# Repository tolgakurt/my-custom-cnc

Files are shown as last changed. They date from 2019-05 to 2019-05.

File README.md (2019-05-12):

# Yet Another CNC Milling Machine

Some time ago I decided that I need a CNC milling machine that would mainly be able to etch and drill PCBs, so that I can prototype faster when building circuits. There were already available, cheap, and similar CNC machines for this purpose, however, most of them had weak spindles and slender frame members which are suitable only to machine PCB materials or acrylic, but I also wanted to machine some other materials as well. There were also some professional grade machines for this purpose, but they were either expensive and overqualified, or didn't meet the specs I required. And most importantly, as a machinery enthusiast I wanted to build one from scratch for fun. Here, I'll try to present my not-so-original design for such a machine.  

## Overall Design

The frame design is very much like those cheap Chinese routers such as [this one](https://www.banggood.com/CNC2418-3-Axis-Mini-DIY-CNC-Router-USB-Wood-Carving-Engraving-Machine-p-1239336.html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). Most of the machines offered by Chinese vendors come with 775 or 755 model spindles which are rated in between 60W and 150W. I wanted the machine to be able to mill other materials like MDF, hard plastics (like PA, PE, POM, etc.), and low grade aluminum. Thus my first modification was to use a [stronger spindle of 400W](https://www.banggood.com/12-48V-400W-ER11-Air-Cooled-Engraver-Spindle-Motor-for-CNC-Carving-p-1269291.html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). Additionally, these routers are mostly built with 20mm by 20mm aluminum Sigma profiles. Since I'll be using a stronger spindle and machining more rigid materials, I went with 30mm by 60mm and 30mm by 30mm sections mostly. Here is the overall view of the machine:  

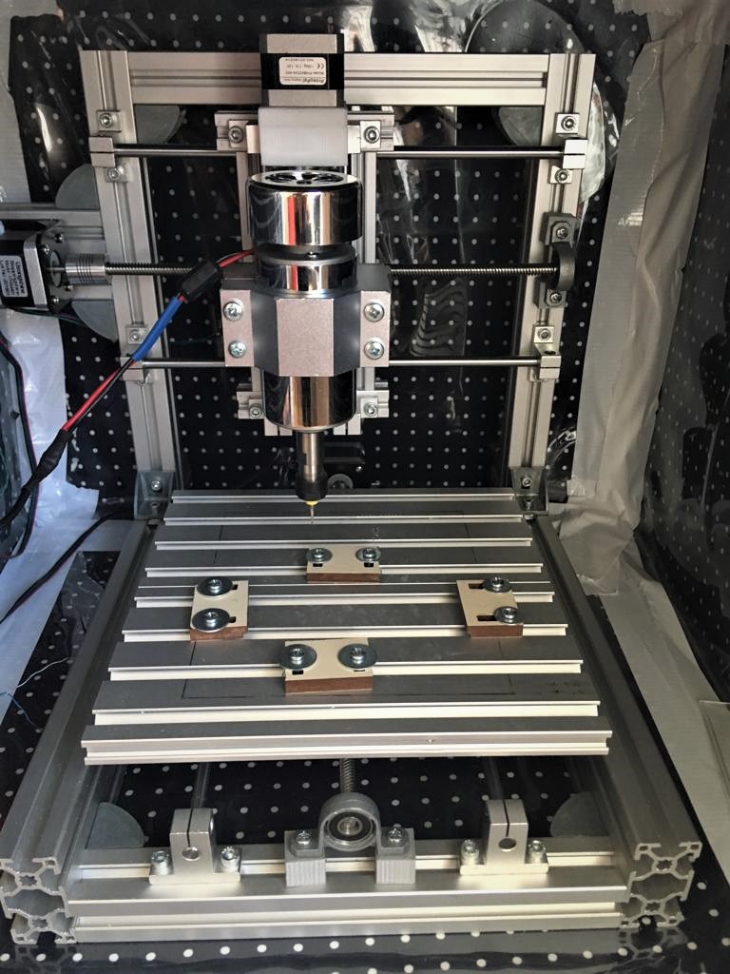
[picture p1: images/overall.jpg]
Overall View


This design offers 20cm by 20cm working area and 10cm of working depth.  

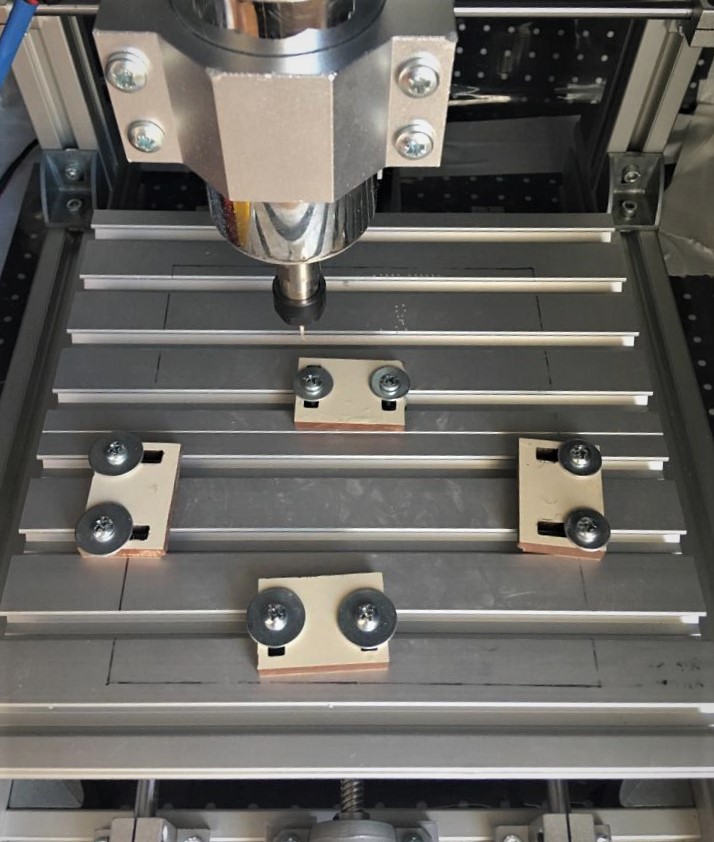
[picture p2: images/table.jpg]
Working Area


The system is mobilized by NEMA17 (specifically 42HS4401) stepper motors, which are driven by A4988 modules embedded into the combination of [an Arduino Uno and a CNC shield](http://osoyoo.com/2017/04/arduino-uno-cnc-shield-v3-0-a4988/). However, I didn't connect the spindle control to the Uno yet, but simply built a box that contains a switch to power it on/off (other switch is for the 3D printer) and adjust the speed manually. One important thing here is that I modified all axes for half steps. This is achieved by connecting some jumpers onto the CNC shield. The details are explained in the link above. The reason of half stepping is to get a better resolution as well as silencing the stepper motors. Half stepping torque of stepper motors is given as 75% of full stepping, so not much loss there. Quarter stepping will make it more silent and accurate, however the torque will decrease around 35% which is too much.  

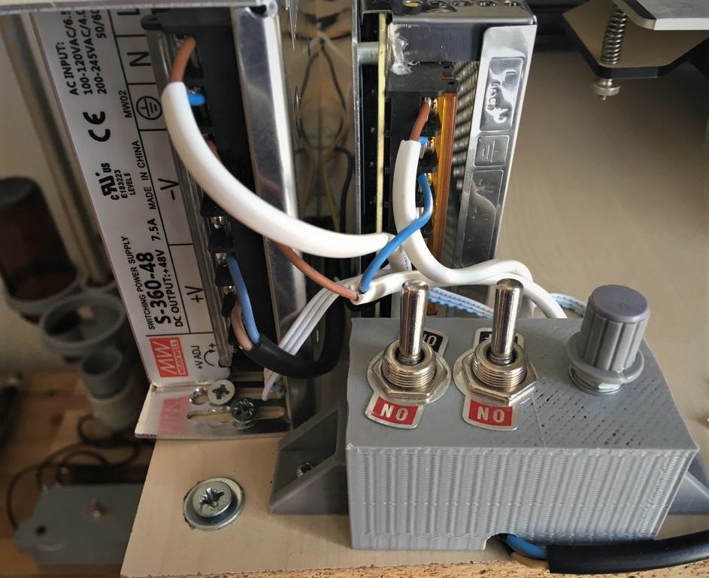
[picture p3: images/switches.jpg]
Switch Box


There are already available 3D printed cases to hold both the Arduino Uno and mentioned shield, and I used [this one](https://www.thingiverse.com/thing:2808019). The case is put outside the enclosed box, since A4988 modules can get dangerously hot inside. I mounted an 8cm fan on top of this case for the same reason. And don't forget to attach tiny heat sinks on top of A4988 modules.  

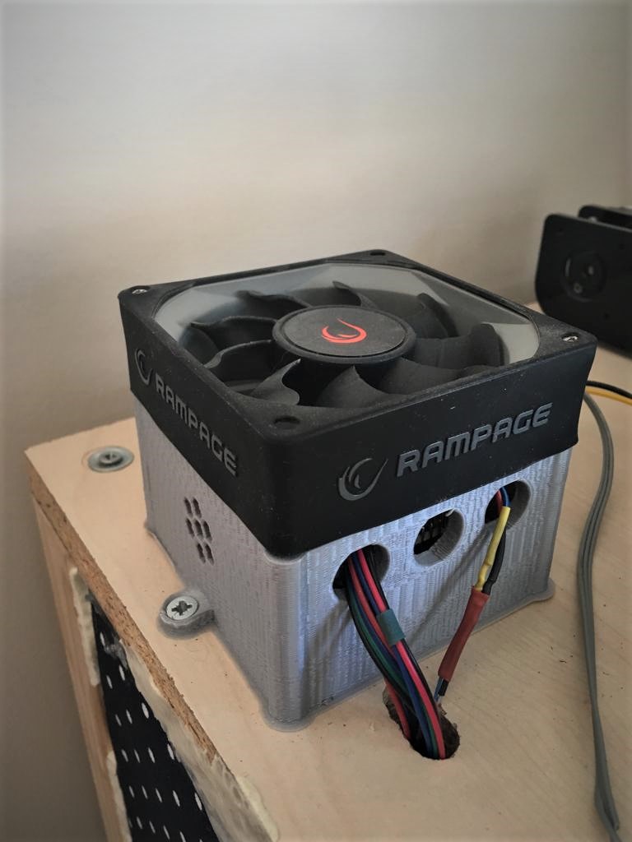
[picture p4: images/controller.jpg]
Case of the Arduino Uno and the CNC Shield


And when all was finished, I realized that the machine makes too much noise to work at night in an apartment. So, I built an ugly-looking, but well-functioning box for sound isolation. It is simply a box with 60cm by 60cm OSB plates, connected with 60cm square wooden legs. Then 6 sides are enclosed by 6 Bondex plates (which is a laminated material with layers foam + rubber + foam as can be seen [here](https://www.adanasesizolasyonu.com/wp-content/uploads/2018/03/Bondex-S%C3%BCnger222.jpg)). I also coated Bondex plates with fabric (as if it's gonna look better) and flexible plastic sheets (so that I can collect the dirt after a milling operation easily). This worked well, except that the machine vibrates the surroundings, so that some noise is regenerated outside the box. What I did was to use some stiff foam as an isolator beneath the box which damped the vibration considerably. According to my phone measurements, the booth drops the noise by 30db, which is enough to keep my neighbors happy.  

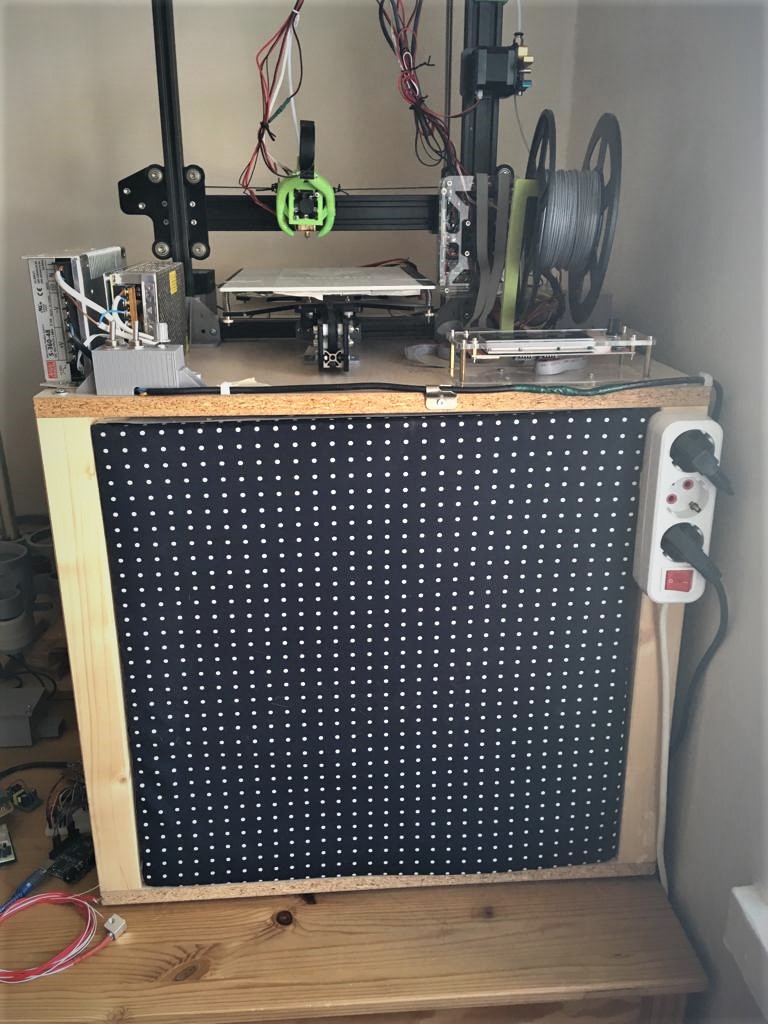
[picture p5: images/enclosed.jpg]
Isolation Booth


And it looks like this in my workshop:  

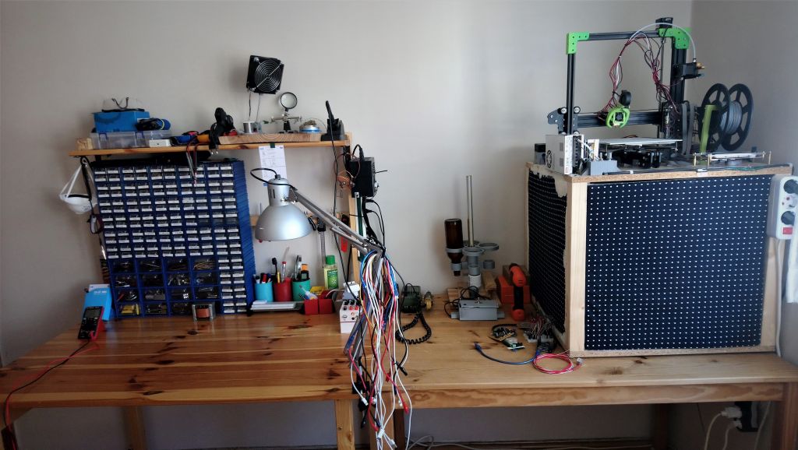
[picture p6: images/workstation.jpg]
My Workshop


## Bill of Materials

### Frame

2x 38cm long [sigma profiles with 30mm by 60mm sections](https://tr.aliexpress.com/item/3D-End-striyel-al-minyum-ala-m-Profil-3060-W-A-r-Al-minyum-3060-W/32987773308.html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)  
3x 25.5cm long [sigma profiles with 30mm by 30mm sections](https://tr.aliexpress.com/item/3D-Yaz-c-Par-alar-3030-Al-minyum-Profil-Avrupa-Standart-Eloksal-Lineer-Ray-Al-minyum/32968908166.html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)  
4x 8.5cm long sigma profiles with 30mm by 30mm sections  
2x 10cm long [sigma profiles with 20mm by 20mm sections](https://tr.aliexpress.com/item/CNC-3D-Printer-Parts-4pcs-lot-European-Standard-Anodized-V-Slot-Linear-Rail-Aluminum-Profile-Extrusion/32813616949.html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,searchweb201602_8_10065_10068_319_10059_10884_317_10887_10696_321_322_10084_453_10083_454_10103_10618_10307_537_536,searchweb201603_52,ppcSwitch_0&algo_expid=79a273b7-c577-4c55-8660-7f41bd6c1b0e-2&algo_pvid=79a273b7-c577-4c55-8660-7f41bd6c1b0e&transAbTest=ae803_4)  
4x 14cm long sigma profiles with 20mm by 20mm sections  
2x 24cm long [sigma profiles with 15mm by 120mm sections](http://www.sigmaprofil.net/15x120-sigma-profile)  
14x [corner connectors for 30mm sigmas](https://tr.aliexpress.com/item/10pcs-of-3030-Corner-Fitting-Angle-30x30-Decorative-Brackets-Aluminum-Profile-Accessories-L-Connector-Fasten-connector/32669590916.htm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,searchweb201602_8_10065_10068_319_10059_10884_317_10887_10696_321_322_10084_453_10083_454_10103_10618_10307_537_536,searchweb201603_52,ppcSwitch_0&algo_expid=9d5dbc37-118d-4f2e-b263-79113ac94142-9&algo_pvid=9d5dbc37-118d-4f2e-b263-79113ac94142&transAbTest=ae803_4)  
4x [corner connectors for 20mm sigmas](https://tr.aliexpress.com/item/10-pcs-25-pcs-al-minyum-2020-k-e-parantez-tertibatlar-20x20x17mm-k-e-a-braketi/32922071230.html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)  

### Rails

2x 18cm long [M8 linear shafts for Z axis](https://www.banggood.com/Outer-Diameter-8mm-x-300380400500mm-Cylinder-Liner-Rail-Linear-Shaft-Optical-Axis-p-993100.html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)  
4x 30cm long M8 linear shafts for XY axes  
1x 18cm long 1.25mm step M8 lead screw for Z axis  
2x 30cm long [8mm step M8 lead screw for XY axes](https://www.banggood.com/T8-8mm-1000mm-Stainless-Steel-Trapezoidal-Lead-Screw-For-3D-Printer-p-1146127.html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)  
12x [SK08 shaft supports](https://aliexpress.com/item/SK08-SK-STAND-UP-Shaft-Support/582520990.html)  
3x [KP08 bearing for lead screw ends](https://tr.banggood.com/8mm-Bore-Diameter-Pillow-Block-Mounted-Ball-Bearing-KP004-Zinc-Alloy-p-976258.html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)  
3x [5mm to 8mm flexible couplings for NEMA17](https://tr.aliexpress.com/item/5-adet-grup-3d-yaz-c-aksesuarlar-5x8mm-veya-5x5mm-z-eksen-Nema-17-23-Step/32840459829.html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)  
3x [M8 anti-backlash nuts for lead screws](https://tr.aliexpress.com/item/T8-Anti-Backlash-Spring-Loaded-Nut-Elimination-Gap-Nut-for-8mm-Acme-Threaded-Rod-Lead-Screws/32808521751.html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,searchweb201602_8_10065_10068_319_10059_10884_317_10887_10696_321_322_10084_453_10083_454_10103_10618_10307_537_536,searchweb201603_52,ppcSwitch_0&algo_expid=3690f36e-8d57-4c15-9ed8-b457cb2fba50-0&algo_pvid=3690f36e-8d57-4c15-9ed8-b457cb2fba50&transAbTest=ae803_4)
8x [LM8UU linear bearings](https://www.banggood.com/LM8UU-8mm-Linear-Ball-Bearing-Bush-Steel-for-CNC-Router-Mill-Machine-p-906777.html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)  
4x [PTFE coated 8mm diameter, 15 mm long linear bearings](https://www.rulmanmarketi.com/urun/pap-0815-p10-teflon-burc-8x10x15-permaglide-burc-3459)  

### Nuts and Bolts

Lots of 10mm long M5 bolts  
Lots of M5 T-nuts for 3030 profile  
Lots of 8mm long M4 bolts  
Lots of M4 T-nuts for 2020 profile  

### Motors
3x NEMA17 stepper similar to [that](https://tr.banggood.com/JKM-42-Hybrid-Stepper-Motor-2-Phase-1_840MM-For-CNC-Router-p-933548.html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)  
2x [NEMA17 motor mounts](https://tr.aliexpress.com/item/NEMA-17-Steppr-Motor-Aksesuarlar-Braketi-Destek-Montaj-L-Tipi-Braketi-Da-42-Step-Motor-Stepping/32919542128.html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)  
1x [400W air cooled spindle motor, clamp, and PS](https://www.banggood.com/400W-12000rpm-ER11-Chuck-CNC-Brushless-Spindle-Motor-with-Driver-Speed-Controller-and-Clamp-p-1149321.html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)  

### Controller
1x [Arduino Uno](https://store.arduino.cc/usa/arduino-uno-rev3)  
1x [Arduino CNC Shield](https://tr.aliexpress.com/item/CNC-kit-for-arduino-CNC-Shield-V3/32829060574.html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,searchweb201602_0_10084_10083_10887_10307_321_453_322_454_10618_536_10065_317_537_10068_319_10059_10103_10884_10696,searchweb201603_0,ppcSwitch_0&algo_pvid=94aba3e1-d1bb-4407-9ae0-063b6d83051e&algo_expid=94aba3e1-d1bb-4407-9ae0-063b6d83051e-0)  
3x [A4988 driver modules](https://tr.aliexpress.com/item/Aokin-A4988-S-r-c-Mod-l-i-in-So-utucu-ile-Step-Motor-S-r/32951539408.html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)  
1x [12V 100W PS for controller and the stepper motors](https://www.banggood.com/AC-220V-To-DC-12V-10A-120W-Power-Supply-Lighting-Transformer-Adapter-Driver-For-Strip-Light-Lamp-p-1145387.html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)  

## Custom Parts

You need to 3D print the parts in the `printedParts` directory. These parts are dimensioned to fit the other parts like SK08, KP08, L8UU, etc.  

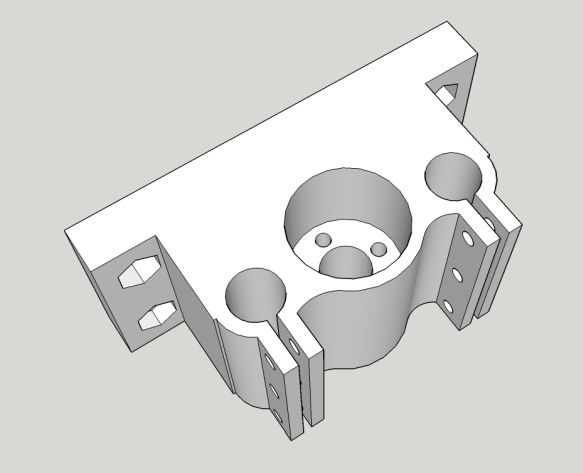
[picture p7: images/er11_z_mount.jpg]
Spindle Clamp Mount


Moving part in Z axis: This part connects the lead screw nut and PTFE coated bearings to the spindle clamp.  

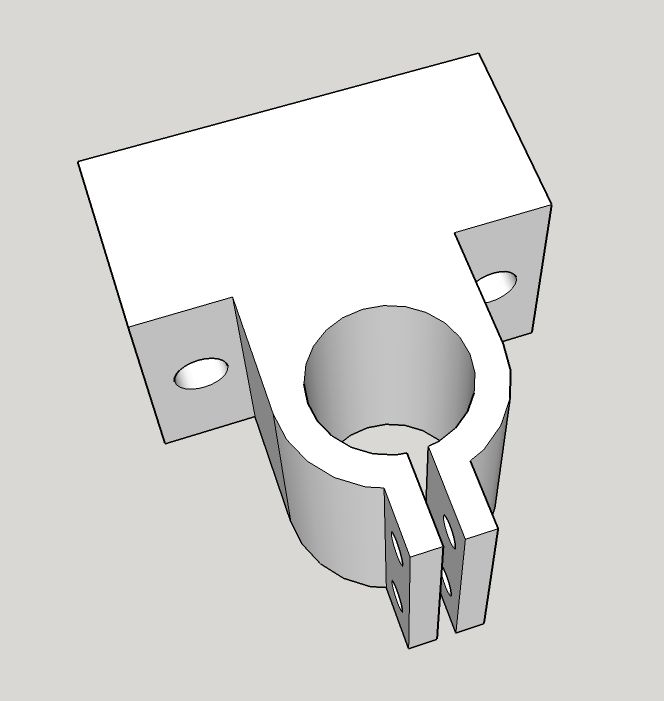
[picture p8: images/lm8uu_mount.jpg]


This part connects LM8UU bearings to the sigma profiles they need to connect to. You should print 8 of these.  

## Assembly

I wish that I can shoot a video that shows the assembly. But it'll be very similar to [this](https://www.youtube.com/watch?v=hB4Cvbtu-lA) or [that](https://www.youtube.com/watch?v=P-zZxicjNww). I'm not sure, maybe some day.  

## Installing Software and Suggested Settings to Operate the Machine

Arduino Uno hosts [GRBL software](https://github.com/grbl/grbl) which routes the machine. To operate the machine from my computer, I use [bCNC](https://github.com/vlachoudis/bCNC), since it's not a gcode sender only, but does offer nice features like probing, autoleveling, gcode editing within a functional user interface.  

The settings I use when I am machining PCB materials is as such:  

Etching feed rates: XY = 250mm/min, Z = 100mm/min  
Z-down when etching: -0.15mm for 30 degree V-bit  

Drill feed rates: Z = 100mm/min  
Drill depth: -1.8mm (or PCB thickness - 0.3mm)

Milling feed rates: XY = 150mm/min, Z = 100mm/min  
Milling depth: -1.5mm (if only perimeter will be milled)  
Milling depth: -0.5mm (if an inner path will be milled)  

## Pictures

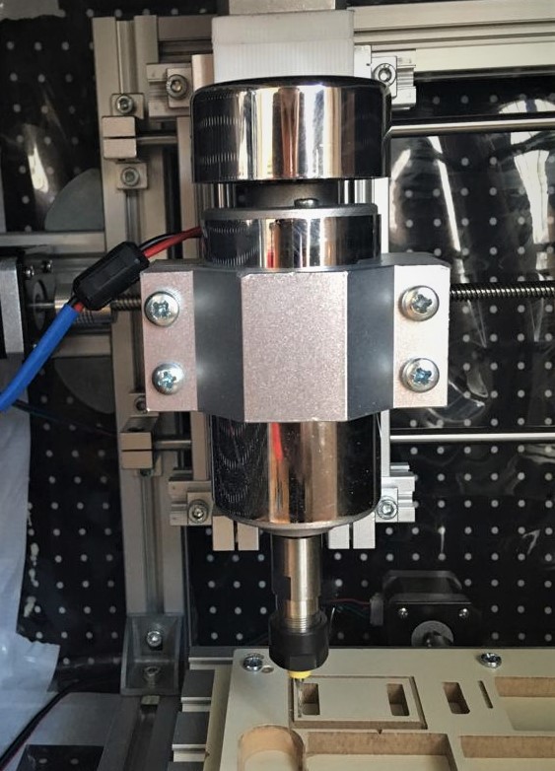
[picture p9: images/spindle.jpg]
Spindle Close-up


Close-up to the spindle.  

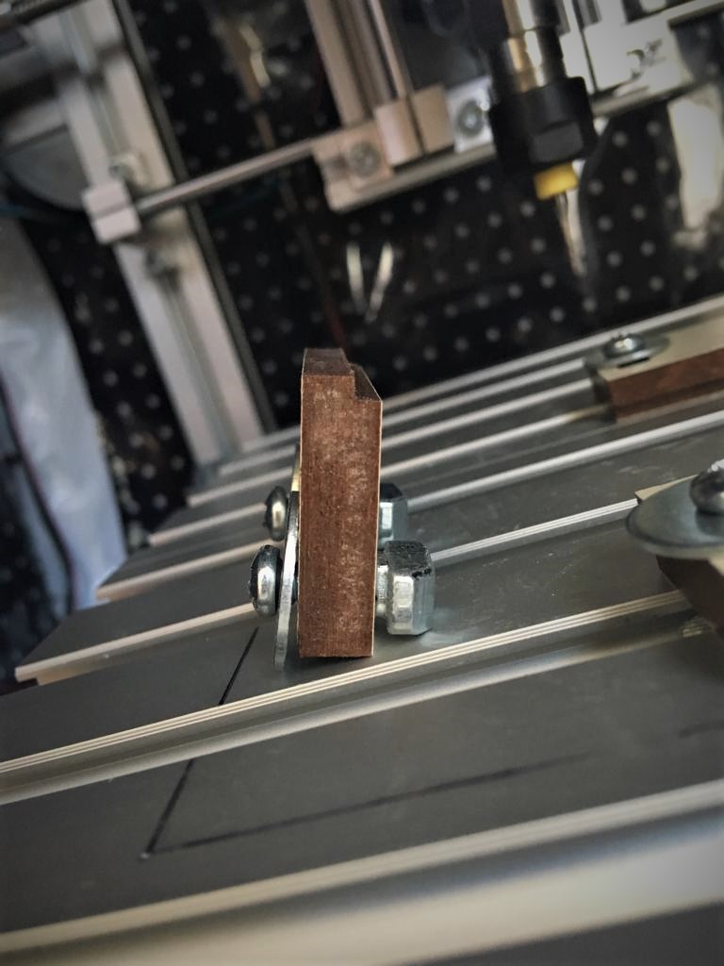
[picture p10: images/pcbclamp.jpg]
PCB Clamps


The clamps I machined out of MDF for PCBs. These clamps have a 3mm cavity to press two PCBs. Why two PCBs? Well, if we use a single PCB put directly above the table and we set the drill depth to 1.5mm, the holes will barely be complete. It's a good practice to drill a bit more than needed to get clean holes. However, if we drill more, the aluminum table will be full of holes soon; and the drill bits may get damages since they are delicate. So, I put a PCB onto another PCB with the same size (the thickness becomes 3mm, thus the cavity in the clamp), and drill down to 1.8mm. So I have collection of dummy PCBs for some common sizes (like 5cm by 10cm, 10cm by 10cm, etc.).  

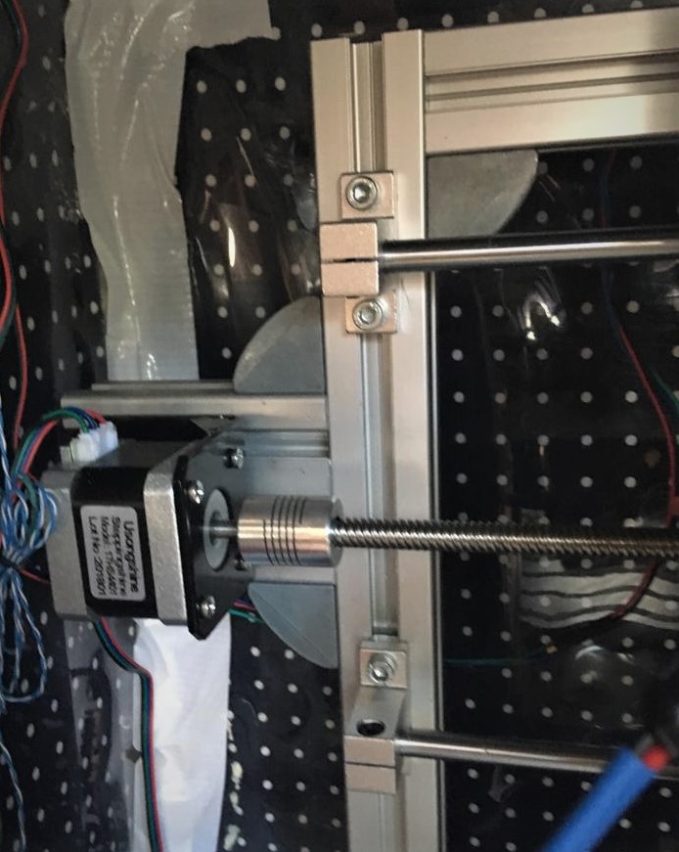
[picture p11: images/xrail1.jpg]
X Rail Left Side

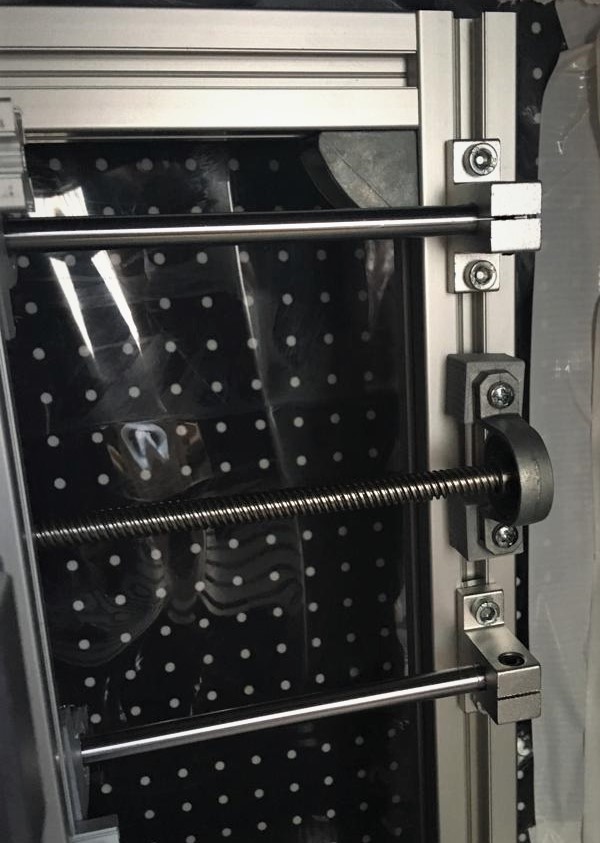
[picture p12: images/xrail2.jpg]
X Rail Right Side


X rail left and right connections.  

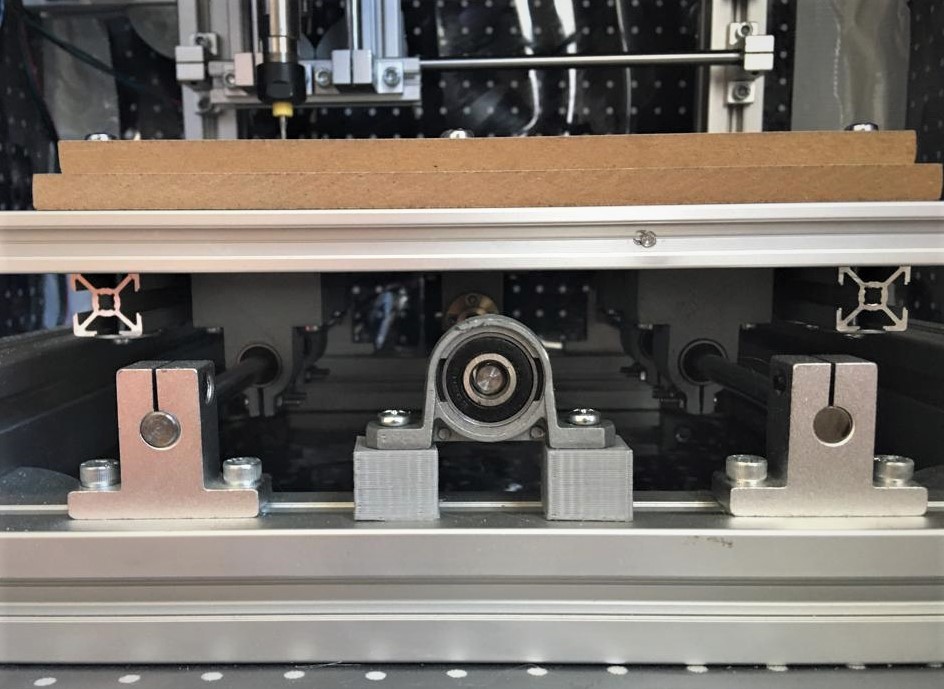
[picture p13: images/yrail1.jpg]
Y Rail Close-up

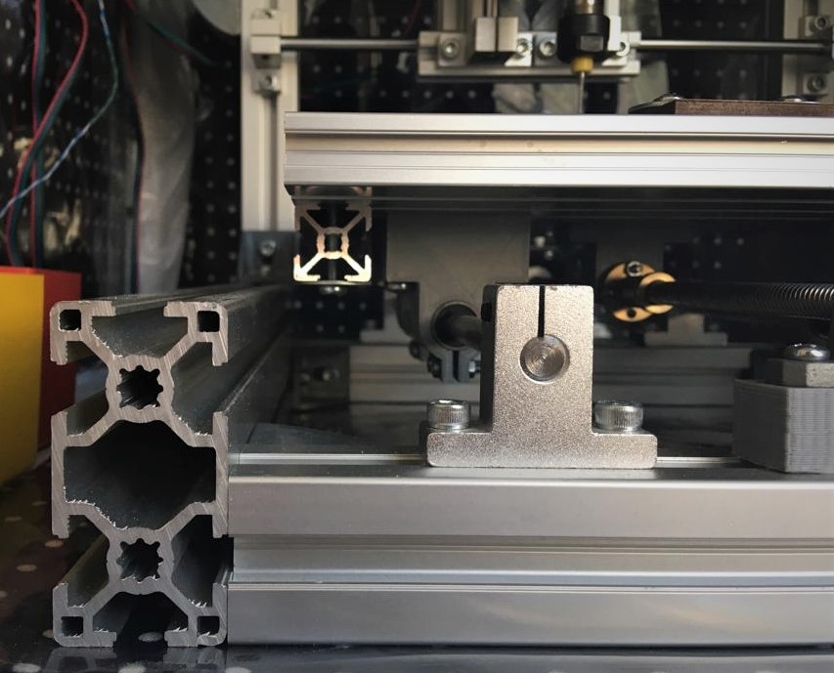
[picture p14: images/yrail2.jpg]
Y Rail Close-up

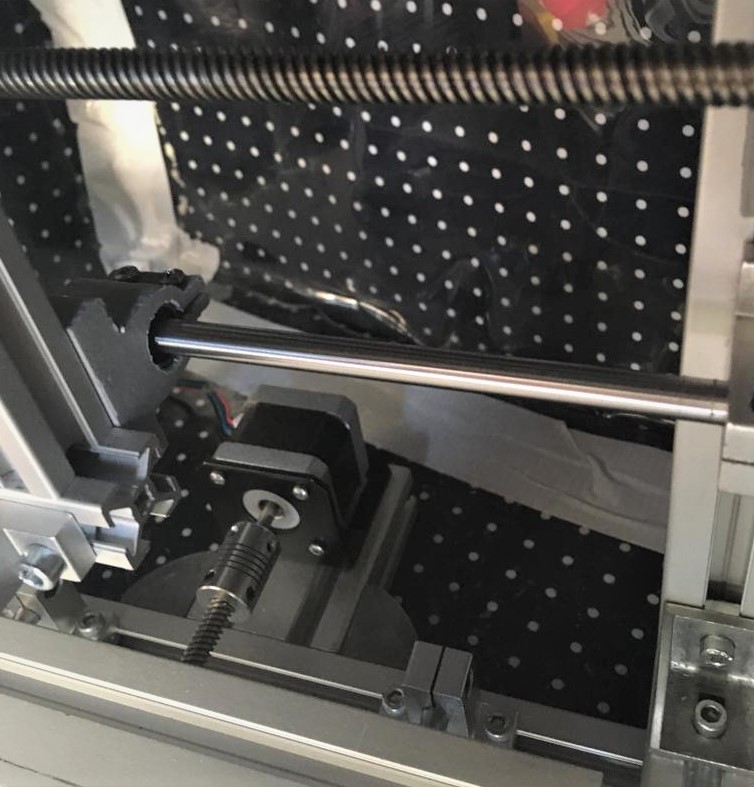
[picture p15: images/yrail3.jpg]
Y Rail Stepper Motor


Y rail close-up and stepper motor.  

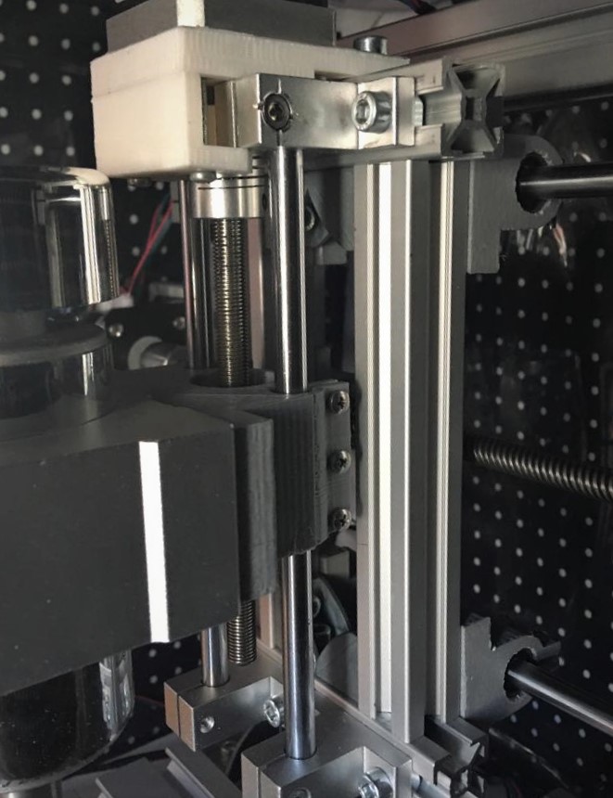
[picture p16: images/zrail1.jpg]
Z Axis From Right

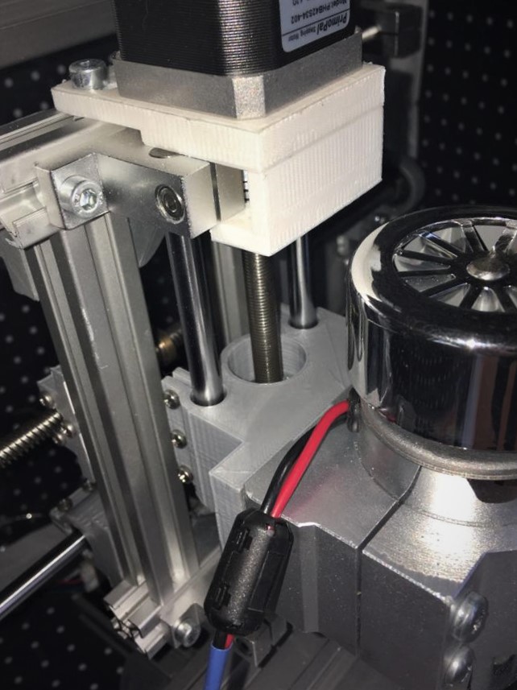
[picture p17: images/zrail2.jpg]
Z Axis From Left


Z axis left and right view.

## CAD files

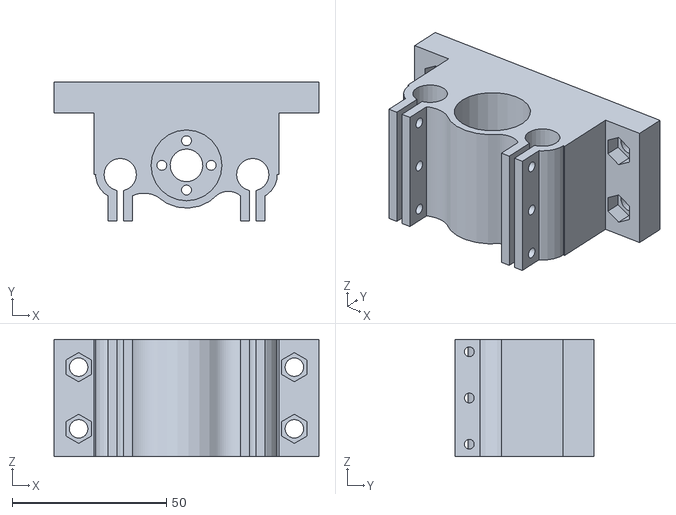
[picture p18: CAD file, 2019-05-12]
printedParts/er11_z_mount.stl
86.0 x 45.0 x 38.0

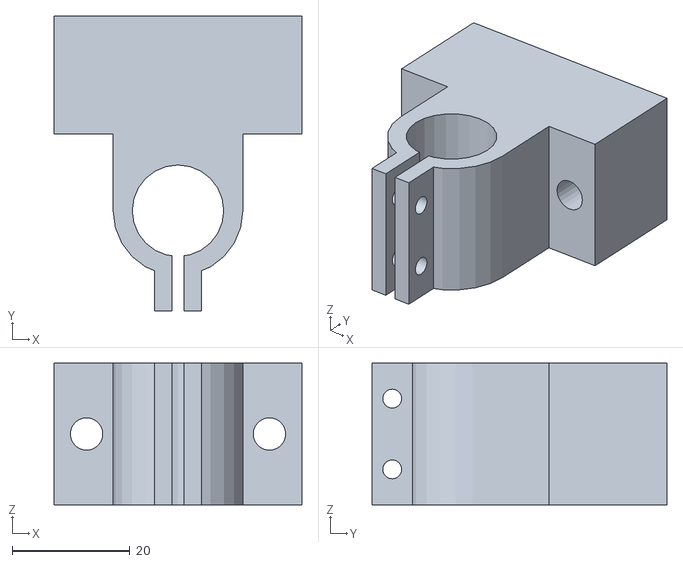
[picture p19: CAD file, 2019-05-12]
printedParts/lm8uu_mount.stl
42.0 x 50.0 x 24.0

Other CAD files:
printedParts/er11_z_mount.skp
printedParts/lm8uu_mount.skp
